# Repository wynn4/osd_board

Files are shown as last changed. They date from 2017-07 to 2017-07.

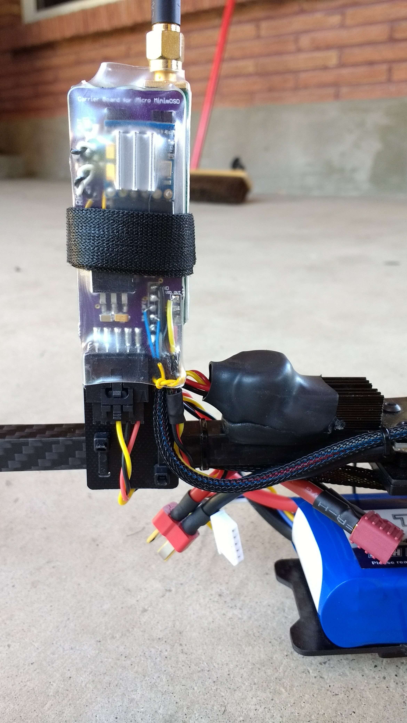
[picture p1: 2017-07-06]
installed.jpg

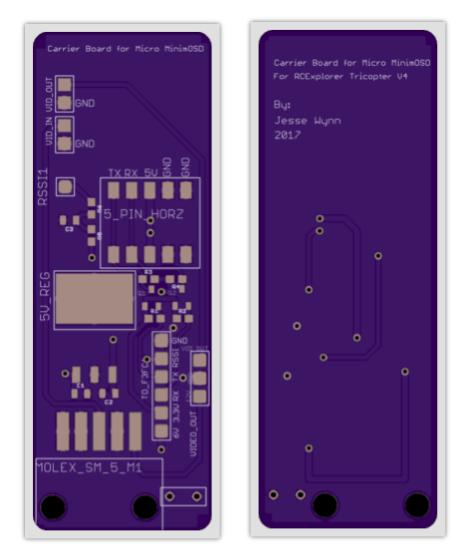
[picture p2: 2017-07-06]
osd_board.jpg

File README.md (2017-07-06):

# osd_board
This is a custom PCB for interfacing between the Micro MinimOSD and the RCE Tricopter V4.  The board is specifically sized to mount on the back side of the V4 fpv transmitter post.  Components for the board can be found by looking at the attached documents.  The voltage regulator should be a SMD packaged LM2940-5 (LDO 5V regulator) and it needs a 0.47uF 0805 package capacitor on the input and a 33uF 0805 capacitor on the output. For more info, see the LM2940 datasheet.  This is the same regulator and capacitor set that was sold for the tricopter power distribution board from RCExplorer.se.  Note: The 5V regulator portion of this circuit is only needed if you are using the 6V or 8V servo power option on the F3FC frame.  The Micro MinimOSD has no voltage regulation so anything above 5V will toast it.

To fabricate your own PCB simply upload the .brd file to oshpark.com

For complete components list, follow this link: http://www.digikey.com/short/30n53w

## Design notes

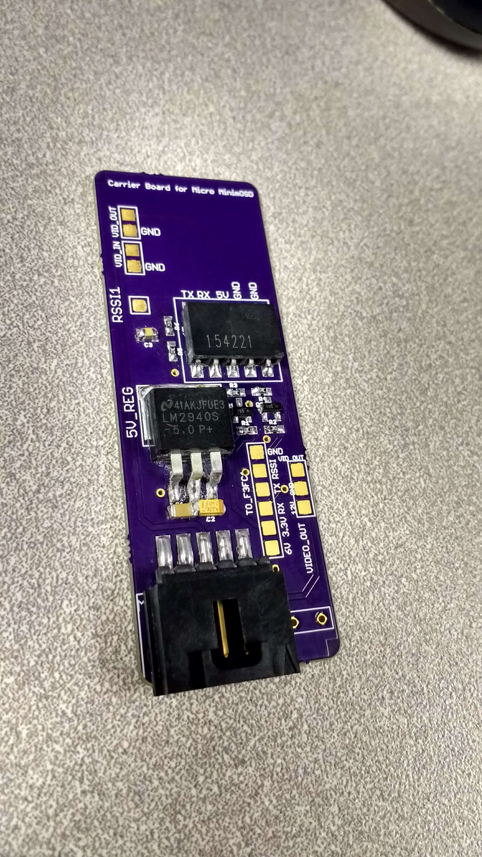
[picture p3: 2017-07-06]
populated_board.jpg

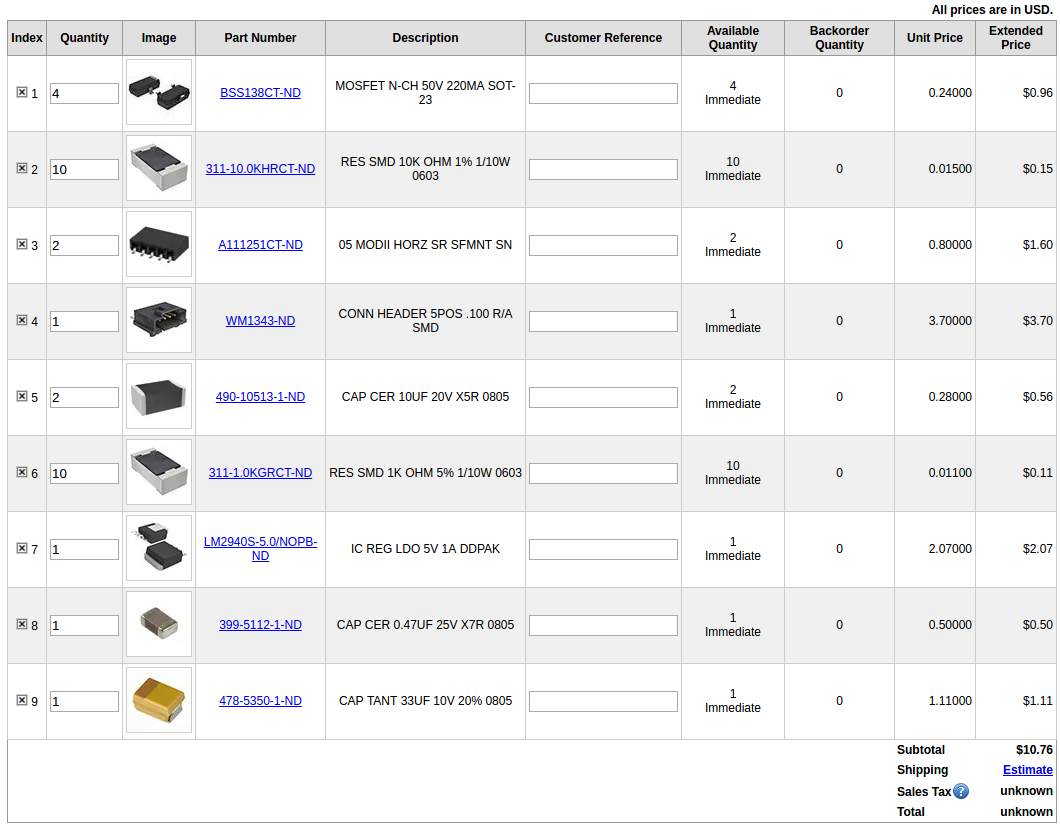
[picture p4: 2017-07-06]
digikey_cart.png

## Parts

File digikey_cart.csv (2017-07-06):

Index | Quantity | Part Number | Description | Customer Reference | Available Quantity | Backorder Quantity | Unit Price USD | Extended Price USD
1 | 4 | BSS138CT-ND | MOSFET N-CH 50V 220MA SOT-23 |  | 4 | 0 | 0.24000 | 0.96
2 | 10 | 311-10.0KHRCT-ND | RES SMD 10K OHM 1% 1/10W 0603 |  | 10 | 0 | 0.01500 | 0.15
3 | 2 | A111251CT-ND | 05 MODII HORZ SR SFMNT SN |  | 2 | 0 | 0.80000 | 1.60
4 | 1 | WM1343-ND | CONN HEADER 5POS .100 R/A SMD |  | 1 | 0 | 3.70000 | 3.70
5 | 2 | 490-10513-1-ND | CAP CER 10UF 20V X5R 0805 |  | 2 | 0 | 0.28000 | 0.56
6 | 10 | 311-1.0KGRCT-ND | RES SMD 1K OHM 5% 1/10W 0603 |  | 10 | 0 | 0.01100 | 0.11
7 | 1 | LM2940S-5.0/NOPB-ND | IC REG LDO 5V 1A DDPAK |  | 1 | 0 | 2.07000 | 2.07
8 | 1 | 399-5112-1-ND | CAP CER 0.47UF 25V X7R 0805 |  | 1 | 0 | 0.50000 | 0.50
9 | 1 | 478-5350-1-ND | CAP TANT 33UF 10V 20% 0805 |  | 1 | 0 | 1.11000 | 1.11

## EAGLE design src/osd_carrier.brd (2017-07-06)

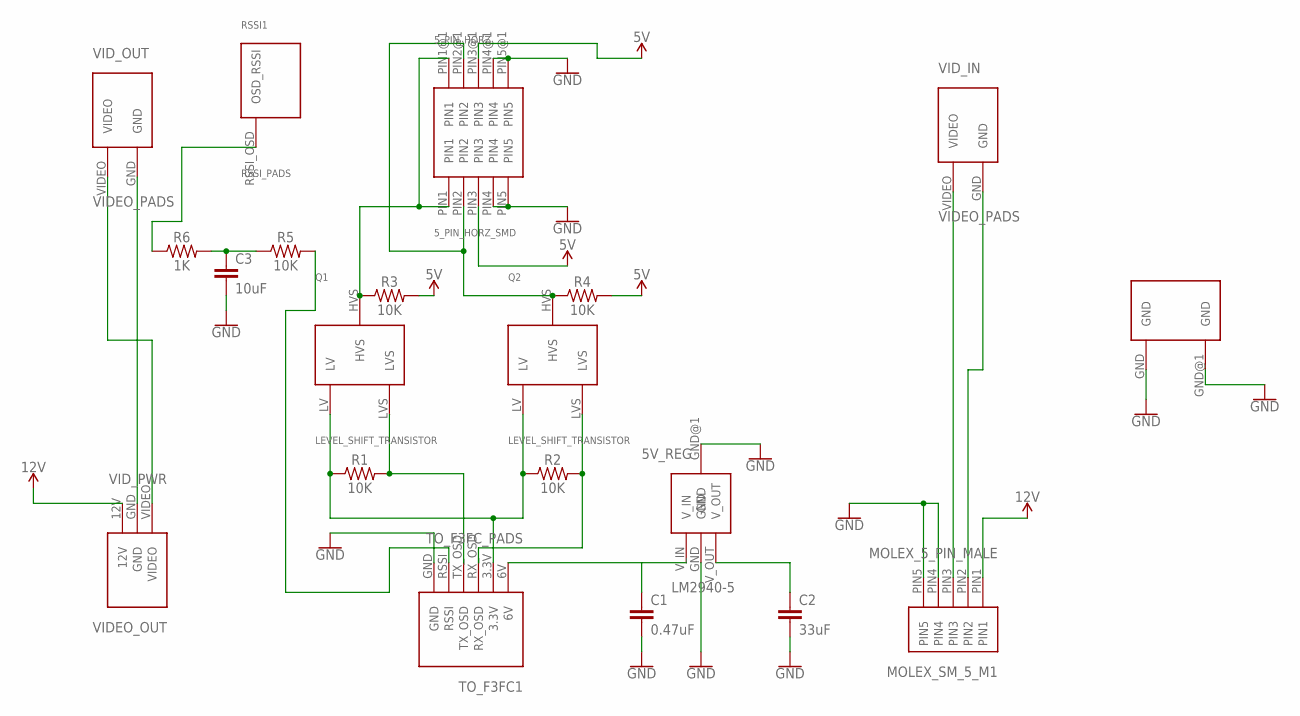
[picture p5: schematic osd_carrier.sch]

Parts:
5V_REG: LM2940-5
5_PIN_HORZ: 5_PIN_HORZ_SMD
ANCHOR1: ANCHOR
C1: 0.47uF; 0805
C2: 33uF; 0805
C3: 10uF; 0805
MOLEX_SM_5_M1: MOLEX_5_PIN_MALE
Q1, Q2: LEVEL_SHIFT_TRANSISTOR
R1, R2, R3, R4, R5: 10K; 0603
R6: 1K; 0603
RSSI1: RSSI_PADS
TO_F3FC1: TO_F3FC_PADS
VIDEO_OUT: VID_PWR
VID_IN: VIDEO_PADS
VID_OUT: VIDEO_PADS

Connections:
3.3V: Q1.LV, Q2.LV, R1.1, R2.1, TO_F3FC1.3.3V
5V: 5V_REG.V_OUT, 5_PIN_HORZ.PIN3, 5_PIN_HORZ.PIN3@1 (PIN3), C2.1, R3.2, R4.2
6V: 5V_REG.V_IN, C1.1, TO_F3FC1.6V
12V: MOLEX_SM_5_M1.PIN1, VIDEO_OUT.12V
D4R_II_RSSI: R5.2, TO_F3FC1.RSSI
GND: 5V_REG.GND, 5V_REG.GND@1 (GND), 5_PIN_HORZ.PIN4, 5_PIN_HORZ.PIN4@1 (PIN4), 5_PIN_HORZ.PIN5, 5_PIN_HORZ.PIN5@1 (PIN5), ANCHOR1.GND, ANCHOR1.GND@1, C1.2, C2.2, C3.2, MOLEX_SM_5_M1.PIN2, MOLEX_SM_5_M1.PIN4, MOLEX_SM_5_M1.PIN5, TO_F3FC1.GND, VIDEO_OUT.GND, VID_IN.GND, VID_OUT.GND
unnamed: C3.1, R5.1, R6.2
unnamed: R6.1, RSSI1.RSSI_OSD
RX_OSD_HV: 5_PIN_HORZ.PIN2, 5_PIN_HORZ.PIN2@1 (PIN2), Q2.HVS, R4.1
RX_OSD_LV: Q2.LVS, R2.2, TO_F3FC1.RX_OSD
TX_OSD_HV: 5_PIN_HORZ.PIN1, 5_PIN_HORZ.PIN1@1 (PIN1), Q1.HVS, R3.1
TX_OSD_LV: Q1.LVS, R1.2, TO_F3FC1.TX_OSD
VIDEO_IN: MOLEX_SM_5_M1.PIN3, VID_IN.VIDEO
VID_OUT: VIDEO_OUT.VIDEO, VID_OUT.VIDEO

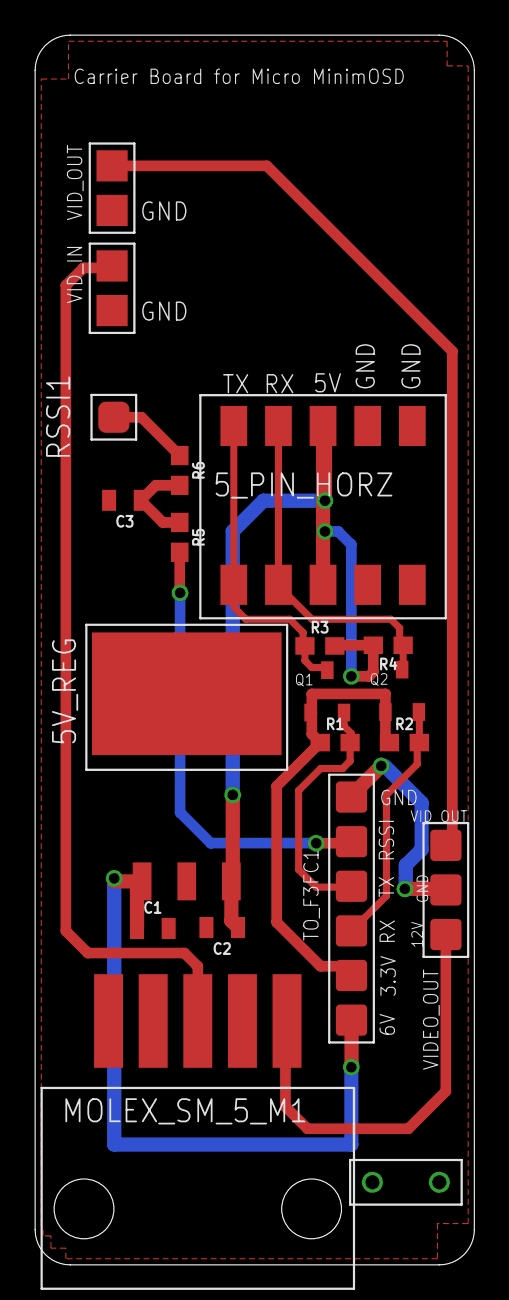
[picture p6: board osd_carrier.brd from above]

Board: 2 copper layers, 25.0 x 70.0 mm, 20 parts (0 on the bottom side), 14 nets.

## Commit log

2017-07-06 added eagle files
    [osd_carrier.brd, osd_carrier.sch]
2017-07-06 organized the repo
    [digikey_cart.csv, osd_carrier.brd, osd_carrier.sch]

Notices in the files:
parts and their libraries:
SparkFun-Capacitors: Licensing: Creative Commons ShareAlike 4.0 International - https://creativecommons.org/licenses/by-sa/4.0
